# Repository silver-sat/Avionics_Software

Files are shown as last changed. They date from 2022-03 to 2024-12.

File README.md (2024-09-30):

# Avionics_Software
This is the SilverSat Avionics board code base, including software for team meeting discussions.

The Avionics Board shares many characteristics with the 
Adafruit Metro M0 Express and in general testing can be performed on either board. However, the standard Arduino Metro M0 Express configuration has fewer serial ports and 
fewer I2C buses than the Avionics Board. Also, serial ports, I2C devices, and digital IO ports 
have different pin locations on the boards. The variants folder in this repository has instructions and configuration files for setting up Metro M0 Express boards with additional serial ports and I2C buses and for setting up the Avionics Board hardware.

## Mock Hardware Drivers
The "AvionicsTesting1" folder contains mock hardware drivers for the components on the Avionics Board. These drivers act as simulated and simplified interfaces for the hardware on the board. They are configured as Arduino libraries.

You can install these libraries by cloning the repository using git or by downloading a .zip file containing the libraries and extracting the folders. Copy the desired libraries into your Ardunio libraries folder.

The interfaces to the mock hardware are designed to be similar to those planned for the flight hardware and software. You can write tests and application software with the expectation of using similar driver interfaces for the flight implementation.

Each library contains an example using the interface to access the mock device. The repository also includes a sketch that exercises each of the mock interfaces.

## Hardware Unit Test Drivers
The "AvionicsTesting2" folder contains test drivers for the hardware components on the Avionics Board. These drivers can be used to verify and exercise the actual devices attached to a Metro M0 or on the board.

You can install these drivers by cloning the repository using git or by downloading a .zip file containing the drivers and extracting the sketches. Follow the instructions in the variants folder to setup the right pin configurations for your environment. If you are using the Avionics Board hardware, define ```CRYSTALLESS``` in the appropriate Arduino core ```startup.c``` file. (The Avionics Board does not have a crystal.) 

You can exercise individual hardware components by building the related sketch (e.g. ```test_imu```) and uploading it to a Metro M0 or the Avionics Board. Note that some external libraries are required, for example to support the MPU6050 hardware. A full list of libraries is in the AvionicsTesting3 folder ```README.md```. Install required libraries following the normal Arduino procedure.

You can execute all of the hardware tests in sequence using a bash script provided in the "AvionicsTesting2" folder. This script requires the Arduino CLI, which can be installed following the instructions at https://arduino.github.io/arduino-cli/0.21/installation/. Make the script executable, connect a serial monitor to the appropriate port on the target board, open a terminal window on your development computer, 
and execute the script. Follow the prompts and observe the results in the serial monitor.

## Test Process Loop
The "AvionicsTesting3" folder "README.md" describes the board testing capabilites of the "test_process_loop" software and provides test setup instructions. The "test_process_loop" sketch in the folder implements the initialization, watchdog management, beacon transmission, command processing, and payload management functions for the Avionics Board.

## FlatSat Testing
The "FlatSat" folder "README.md" describes the flat sat testing capabilities of the "avionics_loop.ino" software and provides test setup instructions. The "avionics_loop.ino" sketch implements the software functions of the Avionics Board. Test routines are provided to test the ground commands received by the satellite and to test the local command interface to the Radio Board.

## Flight

The "Flight" folder "README.md" describes the flight software. This folder contains all of the software used by the flight Avionics Board as well as tests for the Day in the Life scenario and each of the commands recognized by the Avionics Board. The tests are designed for use with pytest and can be repeated automatically using the pytest-repeat plugin.

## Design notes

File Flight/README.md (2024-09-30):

## Avionics Loop
The "avionics" folder contains the Avionics Board software for operating the satellite. 
This includes the process loop, hardware drivers, command processor, and interface software for the antenna, power, radio, and payload boards.

### Test Drivers
The "test_satellite" folder contains drivers for testing the commands supported by the satellite and a "Day in the Life" test.

### Software
The "avionics.ino" sketch is the main process loop for operating the Avionics Board. In avionics.ino, the hardware devices on the Avionics Board are implemented as classes interfacing to real hardware. The other SilverSat boards: Antenna, Power, Radio, and Payload, are implemented as classes which interface with those boards. 

The local messages which Avionics sends to the Radio Board, the ground commands the Radio Board forwards to Avionics, and the responses Avionics sends to the Radio Board for forwarding to the ground are also represented as classes.

The Avionics Board connects to the Radio Board via the Serial1 interface. It connects to the realtime clock via the critical I2C connection. The Avionics Board connects to the IMU, the FRAM, the antenna, and the Power Board via a second I2C connection. Accessing the antenna and the Power Board require activation of an I2C switch. The Avionics Board connects to the Payload Board via digital IO lines.

### Libraries
The "avionics" folder includes an interface to the Arduino log library, which can be used to log status information. Adafruit libaries are used to support the I2C devices, the MPU6050, the FRAM, the real time clock.

### Setup
To setup a build environment, clone this repository to your computer or download a .zip file and extract the folders. Install the Adafruit MPU6050 and FRAM libraries with dependencies using the Arduino Library Manager. Install the ArduinoLog library by downloading it into your library folder. Compile and upload the "avionics.ino" sketch to the Avionics Board microcontroller using a J-Link programmer. There is no bootloader on the Avionics Board.

Review the other READMEs in this repository and ensure your environment is configured correctly. In particular, you will need variant files for the Avionics Board. You will need to define the Avionics Board as crystalless. You will need to modify the linker script to place the executable at location 0 and not leave space for a bootloader. You do not need to set up support for command signing as it has been deprecated.

The "avionics.ino" log level can be changed by modifying the "log.begin" method call in the "avionics_loop.ino" file. The "avionics.ino" file has instrumentation for tracking processing time and memory usage that is enabled by ```#define INSTRUMENTATION```. The log utility is used to display the instrumentation data.

The "avionics.ino" sketch receives commands and sends messages and local commands to and from the Radio Board via the "Serial1" port. It sends log data to the "Serial" port. After uploading your sketch, verify that the Avionics Board has initialized properly by opening a terminal connection to the "Serial" port and reviewing the log entries. Terminal emulators known to work include the Arduino IDE Serial Monitor, the VS Code Arduino extension Serial Monitor, and the tio terminal emulator. (```tio -b 57600 -m INLCRNL,ONLCRNL [portname]```). 

### Testing

You can use the "Serial1" port to send commands to the Avionics Board and observe the responses. The commands must be KISS formatted. Commands use utf-8 single-byte printable characters and can typically be generated by adding FEND [0xC0] at the beginning and end of the command. The first FEND must be following by the appropriate command byte as defined in https://docs.google.com/document/d/1Vwpk0ab0HoC62mU7A1fQwpmhmtmZO0VwPtXjQipe0v0/edit?usp=sharing. Be aware that the FENDs and command bytes are not printable characters. The Avionics Board implements the KISS escape processing protocol, although it is not currently in use.

The "test_satellite" folder includes Python programs for unit testing each of the Avionics Board commands and for a Day in the Life test. These programs are designed to be managed and executed using pytest. After resetting the microcontroller you may run the entire suite of tests by entering ```pytest``` on the command line while in the "test_satellite" directory. (Depending on your configuration, ```python3 -m pytest``` may be required.) pytest also allows selective execution of tests. See https://docs.pytest.org/ for additional information. You can repeat the tests with the pytest-repeat plugin.

In addition to using pytest, you can send and receive traffic on the Serial1 port using a USB adaptor device and tio. Configure tio to display the traffic as hex bytes. 

### Documentation

The SilverSat Avionics Board document in the repository provides an overview of the Avionics Board hardware, software and commands.

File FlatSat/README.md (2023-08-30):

## Avionics Loop
The "FlatSat" folder contains the Avionics Board software for testing and operating the FlatSat configuration. 
This includes the process loop, hardware drivers, command processor, and interface software for the power, radio, and payload boards.

### Test Drivers
The "FlatSat" folder contains drivers for testing
the serial interface with the Radio Board in the "test_avionics" folder. These drivers can be used to test each of the local command implementations that require communication between the Avionics Board and the Radio Board, such as getting radio status and changing radio settings. The test drivers can be used to test the beacon functions and the halt function.

The FlatSat folder also contains
unit test drivers for the command functions of the Avionics Board in the "test_avionics" folder. These drivers can be used to verify and exercise the functions of the Avionics board such as setting the realtime clock, telemetry collection, controlling beacon transmission, and triggering the watchdog.

Also in the "test_avionics" folder are drivers to test the interface with the Payload Board, Power Board, and Antenna. These drivers are augmented by simulators in the "payload_simulator", "eps_simulator", and "antenna_simulator" folders, which contain Python programs suitable for execution on an Adafruit Metro M0 (payload) and Adafruit Grand Central (eps and antenna). When appropriately connected, these simulators respond to the interfaces similarly to the actual devices, thus allowing testing without the entire Flatsat configuration. The folders also include simple programs for testing the simulators.

### Software
The "avionics_loop.ino" sketch is the main process loop for testing and operating the Avionics Board. In avionics_loop, the hardware devices on the Avionics Board are implemented as classes interfacing to real hardware. The other SilverSat boards: Power, Radio, and Payload, are implemented as classes which interface with those boards. 

The local messages which Avionics sends to the Radio Board, the ground commands the Radio Board forwards to Avionics, and the responses Avionics sends to the Radio Board for forwarding to the ground are also represented as classes.

The Avionics Board connects to the Radio Board via the Serial1 interface. It connects to the realtime clock via the critical I2C connection. The Avionics Board connects to the IMU, the FRAM, the antenna, and the Power Board via a second I2C connection. Accessing the antenna and the Power Board require activation of an I2C switch. The Avionics Board connects to the Payload Board via digital IO lines.

### Libraries
The "FlatSat" folder includes an interface to the Arduino log library, which can be used to log status information on the Radio Board Serial interface. Adafruit libaries are used to support the I2C devices, the MPU6050, the FRAM, the real time clock,  The Arduino Crypto library is used to support command signing.

### Setup
Signed commands require that the Avionics Board and the ground share a secret. This secret is defined as a sixteen-byte array. 

Following the Arduino convention, an "arduino_secrets.h" file is required to store the secret. It must ```#define``` a sixteen-byte array named ```SECRET_HASH_KEY```, which is compiled into the sketch. DO NOT upload "arduino_secrets.h" to github or other shared locations. The software used to generate signed commands must use an identical sixteen-byte secret. For these tests, the secret is stored in "secret.txt". DO NOT upload "secret.txt" to github. The "test_signing" folder located in the "AvionicsTesting3" folder in this repository includes a Python program, "make_secret.py", which can be used to generate shared secrets. If the secrets use by the Avionics Board and the test programs or ground software are not identical, command signing will fail.

To setup a test environment, clone this repository to your computer or download a .zip file and extract the folders. Generate a secret and create an "arduino_secrets.h" file and a "secret.txt" file to store it. Add both to your ```.gitignore``` to prevent them from being uploaded to github. Install the Adafruit MPU6050 and FRAM libraries with dependencies using the Arduino Library Manager. Install the ArduinoLog and Arduino Crypto libraries by downloading and copying them into your library folder. Compile and upload the "avionics_loop.ino" sketch to the Avionics Board microcontroller using the standard Arduino tools or alternative deployment tools.

The "avionics_loop.ino" sketch has extensive logging capabilities based on the ArduinoLog utility (https://github.com/thijse/Arduino-Log/). The log level can be changed by modifying the "log.begin" method call in the "avionics_loop.ino" file. 

The "avionics_loop.ino" file has instrumentation for tracking processing time and memory usage that is enabled by ```#define INSTRUMENTATION```. The log utility is used to display the instrumentation data.

The "avionics_loop" sketch receives commands and sends messages and local commands to and from the Radion Board via the "Serial1" port. It sends log data to the "Serial" port. After uploading your sketch, verify that the Avionics Board has initialized properly by opening a terminal connection to the "Serial" port and reviewing the log entries. Terminal emulators known to work include the Arduino IDE Serial Monitor, the VS Code Arduino extension Serial Monitor, and the tio terminal emulator. (```tio -m INLCRNL [portname]```). If you are using a bootloader, be aware that use of
a serial monitor can interfere with uploading. If you aren't using the Arduino toolset, disconnect your serial monitor software before using the bootloader.

### Testing

You can use the "Serial1" port to send commands to the Avionics Board and observe the responses. The commands must be KISS formatted. Since commands in general use utf-8 single-byte printable characters, commands can typically be generated by adding FEND [0xC0] at the front and end of the command. The first FEND must be following by the appropriate command byte as defined in https://docs.google.com/document/d/1Vwpk0ab0HoC62mU7A1fQwpmhmtmZO0VwPtXjQipe0v0/edit?usp=sharing. Be aware that the command bytes are not printable characters.

The Avionics Board implements the KISS escape processing protocol, although it is not currently in use.

The "FlatSat/test_avionics" folder includes python programs for unit testing each of the Avionics Board commands and for interfacing to the rest of the satellite. These programs are designed to be managed and executed using pytest. After resetting the microcontroller you may run the entire suite of tests by entering ```pytest``` on the command line while in the "FlatSat/test_avionics" directory. (Depending on your configuration, ```python3 -m pytest``` may be required.) 

pytest also allows selective execution of tests. See https://docs.pytest.org/ for additional information. Be sure to run the ```test_00_avionics_initialization.py``` test first any time the microcontroller is restarted to process the initialization messages. You can also review the startup messages in a serial monitor and then end the serial monitor session before running automated tests. To test signed commands, the "secret.txt" file must include the same secret as the "arduino_secrets.h" file used to build "avionics_loop.ino." The "utility.py" program in "avionics_test" contains functions to issue commands and to generate signed commands. 

You can observe traffic on the Serial1 port using a USB adaptor device and tio. ```tio -x [portname]``` will display the traffice as hex bytes. Note that this will interfere with the automated tests, so should only be used when manually entering commands on the (separate) Serial port. It may also be useful to open terminals showing output from the payload simulator and the eps/antenna simulator.

### Documentation

The SilverSat Avionics Board document in the repository provides an overview of the Avionics Board hardware, software and commands.

Documentation for the software and tests can be viewed by running doxygen (https://doxygen.nl/) using the provided Doxyfile and then opening docs/index.html in a browser. Modifications to the Doxyfile may be required to reflect your directory structure.

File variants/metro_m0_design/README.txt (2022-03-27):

This folder contains the variant files for the Adafruit Metro M0 Express to add 2 extra HW serial ports (3 total) and 1 extra wire port (2 total).

Put these in the appropriate variants folder.  For example on my system it was:

C:\Users\conra\AppData\Local\arduino15\packages\adafruit\hardware\samd\1.7.10\variants\metro_m0

The fritzing file "MetroVariantTest.fzz", shows roughly (I used cables instead of FTDI modules) how I connected to the Metro M0 to test the new ports.

I will be adding code (Arduino) later that supports the test.

I chose the two I2C devices simply based on what was lying on my bench at the moment, so there's nothing special about them.

For this variant:
Serial0 is on D11 (txd) and D13 (rxd)
Serial1 is on D1 (txd) and D0 (rxd) (default config)
Serial2 is on D6 (txd) and D7 (rxd) 
Wire uses SCL and SDA (by default, obviously)
Wire1 is on D4 (SDA) and D3 (SCL)

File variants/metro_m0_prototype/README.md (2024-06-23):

This folder contains the variant.cpp and variant.h files for the Adafruit Metro M0 used to prototype the SilverSat Avionics Board. 

These files are not compatible with the Avionics Board. To build Arduino sketches for the Avionics Board, see the avionics_board variants.

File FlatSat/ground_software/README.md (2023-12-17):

# Ground Control Software

The ground control software presents a user interface for entering commands to the satellite and receiving responses. It also enables the use of gpredict radio Doppler data for the ground radio.

The ground control software is a web application designed to run on a Flask development server in a single-threaded environment on a single laptop. It is not secured for network deployment and the serial link to the ground radio is not implemented for use in a multi-threaded environment.

## Installing the User Interface

Clone the Avionics_Software repository from github to a local directory on the laptop. If the repository is already present, ensure it is up to date using git pull or the equivalent.

Open a command shell and navigate to the ground_software directory in the FlatSat directory. Create a python virtual environment with the following command

```python3 -m venv .venv```

Activate the virtual environment with 

```. .venv/bin/activate```

Note that the .venv directory is a hidden file (it starts with "."), so you may have to use command line options or change the settings of your file manager to see it in a file listing.

Now install Flask using this command

```pip install Flask```

Python virtual environments are recommended for use with Flask, and may be required by your operating system. If you understand the implications, you may be able to install Flask at the system level using a package manager or other method.

Install pyserial using this command

```pip install pyserial```

Now move to the control directory in the ground_software directory and enter the following command

```Flask run --debug```

This starts the app.py application in the folder. If you receive an error message, you may need to modify the serial port name in app.py to match the port name on your system.

Open a browser and navigate to the address displayed, typically http://127.0.0.1:5000/

You may now enter commands to the satellite by clicking a button or typing a command on the command line.

## Installing the Radio Doppler Control

Install the gpredict application on the laptop following the instructions for the operating system.

The gpredict_radio_interface.py program in the radio folder and the Flask web application provide the functions of Hamlib rigctld daemon. You do not need rigctld to control the radio frequency.

Open a new command window, navigate to the radio folder, and enter the command

```gpredict_radio_interface.py```

The program will listen on the default TCP/IP port used by gpredict for radio frequency information.

Now launch gpredict, add a radio as explained in the User Manual, open the radio interface, select a satellite in Target and track it. Verify that the Flask application is running. Select your radio in Settings and engage it. Radio Doppler data for the selected satellite will be transmitted to the ground radio.

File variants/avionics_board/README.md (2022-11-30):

This folder contains the variant.cpp and variant.h files for the SilverSat Avionics Board. 

To build Arduino sketches for the Avionics Board or to test using a Metro M0, git clone or download a .zip file containing these files to your development computer. 
Create a hardware folder in your Arduino sketch folder as documented 
at https://arduino.github.io/arduino-cli/0.21/platform-specification/#hardware-folders-structure, copying the Adafruit Metro M0 Express
files as the hardware configuration template.

Rename the appropriate folders and make the necessary changes to boards.txt in the new folder structure. Copy variant.cpp and variant.h
into that folder structure, replacing the Metro M0 Express files with the same names.

As an example, on Ubuntu, create a "hardware" folder in your "Arduino" folder. Create an "avionics" folder in "hardware."
Copy the "samd/[version]" folder containing the Metro M0 definitions located at ".arduino15/packages/adafruit/hardware/samd/[version]" to 
your new "hardware" folder and rename it to "samd." (That is, drop the version level of the folder structure.) Rename the "metro_m0" folder in the 
"variants" folder and edit "boards.txt" to reflect the new name. Replace "variant.cpp" and "variant.h" in the renamed folder with the
downloaded files. Follow a similar process to create a Metro M0 configuration with additional serial ports and a second I2C bus for testing. 

If you do not have the Metro M0 Express definitions on your development computer, you can download them using the procedure
documented at https://learn.adafruit.com/adafruit-metro-m0-express/arduino-ide-setup.

Define ```CRYSTALLESS``` in the Avionics Board Arduino core startup.c file. (The Avionics Board does not have a crystal.) Do not make this change for Metro M0.

If you want to load software using a programmer and have no bootloader on the board, modify the "boards.txt" file to make "flash_without_bootloader.ld"
the linker script file base name. This provides reliability and convenience, but does require that you have a hardware programming device. Be aware that your program 
should be loaded at 0x2000 if using a bootloader and will likely be loaded at 0x0000 if not.

After you have setup the definitions for the Avionics Board, open your development environment, select the new board configuration, 
build your sketch, and upload it to the Avionics Board. See the instructions in the AvionicsTesting3 ```README.md``` for further information.

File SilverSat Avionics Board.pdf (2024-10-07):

# SilverSat Avionics Board

Software and Command Description

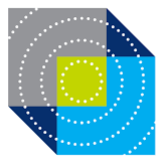
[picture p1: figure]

7 October 2024
Contact: lee@silversat.org

## INTRODUCTION

This document summarizes the hardware and software of the SilverSat Avionics Board. It briefly describes the interfaces with the SilverSat Power Board, Radio Board, Payload Board, and antenna. It also provides an overview of the commands received and sent by the Avionics Board.

1

## REVISION HISTORY

Version 1.0, Apr 11, 2023

Initial release

Version 1.1 Apr 14, 2023

Added command formats, reorganized sources

Version 1.2

Reformatted command outputs

Version 1.3 October 7, 2024

General update to reflect software changes

2

## TABLE OF CONTENTS

INTRODUCTION
REVISION HISTORY
TABLE OF CONTENTS
OVERVIEW
HARDWARE
SOFTWARE
INITIALIZATION
PROCESS LOOP
SOFTWARE ORGANIZATION
TESTING INFRASTRUCTURE
AVIONICS BOARD HARDWARE
MICROCONTROLLER
WATCHDOG
REAL TIMWATCHDOGE (https://docs.google.com/document/d/1S8KbOSXrL_yW1S88hW_mSTv4Je4pVHNBBO4vtaCxD2I/edit) CLOCK
INERTIAL MANAGEMENT UNIT
FRAM
POWER BOARD INTERFACE
RADIO BOARD INTERFACE
SATELLITE COMMANDS
GROUND COMMANDS
CHANGE SATELLITE STATE
COMMAND
PARAMETERS
DESCRIPTION
GET SATELLITE STATE
COMMAND
PARAMETERS
DESCRIPTION
INVOKE SATELLITE OPERATION COMMAND
PARAMETERS
DESCRIPTION
INVALID AND UNKNOWN COMMANDS COMMAND
PARAMETERS
DESCRIPTION

3

RADIO COMMANDS
COMMAND
PARAMETERS
DESCRIPTION
DEPRECATED COMMANDS
COMMAND
PARAMETERS
DESCRIPTION
COMMAND FORMATS
COMMAND
FORMAT
ACK
RESPONSE
LOCAL COMMANDS
COMMAND
VALUE
PAYLOAD BOARD INTERFACE
ANTENNA INTERFACE
SOURCES
TOOLS
LIBRARIES
REFERENCES
LEARNING

4

## OVERVIEW

SilverSat is an educational project for students in middle school and high school. The students are building and programming a 1U cubesat that will take photos from space and transmit them to a widely available media service, currently planned to be Twitter. SilverSat will launch from the International Space Station courtesy of an educational grant from NASA.

## HARDWARE

SilverSat hardware includes an EnduroSat structure surrounded by solar cells and four boards implementing the satellite capabilities. The boards are:

1. An EPS-I power board, also provided by EnduroSat, which stores power from the solar cells surrounding the structure and manages the distribution of power to the satellite
2. An Avionics Board, described in this document, which manages the timing of photo and communications on the Payload Board, processes commands from the ground, and manages the timing and content of beacon broadcasts
3. A Radio Board, which manages communications between the satellite and the ground station
4. A Payload Board, which captures images and communicates them to a media service, currently Twitter.

The Avionics Board, the Radio Board, and the Payload Board are developed and implemented by SilverSat. The antenna used by the satellite is provided by EnduroSat.

This document focuses on the hardware and software located on and accessed by the Avionics Board, including its microcontroller, watchdog timer, realtime clock, inertial measurement unit, and ferroelectric random-access memory. It also describes the interfaces to the Power Board, the Radio Board, the Payload Board, and antenna.

## SOFTWARE

The software running on the Avionics Board implements initialization, services the watchdog, manages beacon timing, executes commands from the ground, and controls the Payload Board. The software is implemented using the Arduino software

5

environment and is based on the standard setup() and loop() functions provided by Arduino.

### INITIALIZATION

When power is applied to the Avionics Board, the avionics loop software starts the Serial and logging functions used for board software development, monitoring, and testing. These functions may not be used in the flight software, depending on the final checkout procedures selected by the team.

The avionics loop then initializes the Avionics Board and the interfaces to the Power Board, the Radio Board, and the Payload Board.

The Avionics Board then pauses for a predefined deployment delay interval. In the flight software, this delay will be 45 minutes.

After the delay interval, the Avionics Board deploys the antenna, waiting to verify that deployment is successful. In sequence, the Avionics Board attempts two deployments using the I2C interface to the antenna and signals the Radio Board to attempt two deployments using a direct connection to the antenna. Initialization proceeds when the antenna shows that it has been opened successfully.

The Avionics Board then commences its standard process loop.

### PROCESS LOOP

The process loop, instantiated in the Arduino loop() function in avionics_loop.ino, includes the following steps:

1. Determine whether the process is within the watchdog window. If so, trigger the watchdog.
2. Check the IMU to determine whether the satellite is stable.
3. Determine whether the beacon interval has elapsed. If so, send a beacon.
4. Determine whether a command has arrived from the ground or the Radio Board. If so, process the command.
5. Determine whether it is time to take a photo. If so, signal the Payload Board to take the photo.
6. Determine whether the Payload Board is requesting a shutdown. If so, turn off power to the Payload Board after a delay.

The process then repeats.

### SOFTWARE ORGANIZATION

6

In addition to the overall structure provided by the Arduino setup() and loop() functions in the avionics.ino file, the software is organized into classes providing the required capabilities. Most classes are declared in a header file and defined in a cpp file. The exceptions are the Beacon, Message, and Response classes which are header only.

The PowerBoard, AvionicsBoard, RadioBoard, PayloadBoard, and Antenna functions and data are defined as classes.

Hardware such as the EPS-I power supply and the DS1337 real time clock are defined as classes. Some hardware has an additional abstraction and encapsulation layer, for example the PowerBoard and the ExternalRTC, respectively, for the devices just noted. This is also the case for the ExternalWatchdog and the IMU.

Command processing is controlled by the CommandProcessor class, which acquires commands from the RadioBoard, validates and parses them and retrieves a command object from the CommandWarehouse class. The CommandProcessor then executes the acknowledgement and processing methods in the command object, taking advantage of the virtual function capability provided by the C++ language.

The log_utility class generates standard log entries to support the development process. Logging will not be included in the flight software unless it is required for final testing after the vibration test.

### TESTING INFRASTRUCTURE

The silver-sat/Avionics_Software github repository contains versions of the software used for prototyping, unit testing, and function testing in the AvionicsTesting1, AvionicsTesting2, and AvionicsTesting3 directories. The readme files in those directories provide additional information.

The FlatSat testing version of the software is located in the FlatSat directory in the repository. In addition to the avionics_loop software, it also contains test simulators for the Antenna, the Power Board, and the Payload Board. An extensive set of tests for initialization, board interfaces, commands, and error conditions are located in the test_avionics directory.

The Flight directory contains the flight version of the software, implemented with avionics.ino as the main sketch. Test cases are provided in the test_satellite directory.

These tests are structured to be run as a complete set beginning with board initialization or can be run individually. They are written in Python and use pytest as the test driver. A

7

common.py module provides convenience functions. Instructions for setting up and executing the tests are in the readme.

Also present in the repository is a Doxygen file that can be used to generate detailed documentation of the software. Again, instructions are in the readme.

## AVIONICS BOARD HARDWARE

The Avionics Board hardware is defined in the Avionics Board (https://github.com/silver-sat/Avionics_Board.git) repository.

The microcontroller is a Microchip SAMD21G18 32-bit Cortex-M0+ with 256K of flash and 32K of random access memory. The microcontroller runs the avionics loop software in the Arduino runtime environment. The Avionics Board includes an external Texas Instruments TPS3813-Q1 watchdog timer, a Maxim Integrated DS1337 real time clock, an Adafruit MPU-6050 inertial management unit, an Infineon Technologies 32K byte CT15B256J ferroelectric random access memory, and switches to control access to external I2C devices and two serial links. The critical I2C for the realtime clock and the microcontroller serial link are always enabled.

### MICROCONTROLLER

The microcontroller pins are defined in the Arduino variant.h and variant.cpp files in the repository. There is no crystal on the Avionics Board, and the Ardunio environment must be configured to reflect that. The microcontroller software can use a bootloader or can be programmed with a hardware device.

If a bootloader is used, it must be aware of the watchdog and either trigger or disable it during program loading. The load address of the software must be updated to reflect the presence or absence of a bootloader. Recent versions of the software have used a J-Link EDU Mini to program the Avionics Board to avoid problems with the bootloader and watchdog interaction.

A timer in the microcontroller is used for beacon interval timing. The internal real time counter is not used in this capacity, thus enabling beacons before the clock is set. The internal watchdog in the microcontroller is not used.

### WATCHDOG

The external watchdog provides a lower bound and an upper bound for a window and must be triggered within the window to prevent a reset. Because the watchdog is always active, the appropriate resistor must be shorted to enable software loading on the flight

8

hardware.

### REAL TIME CLOCK

The DS1337 provides real time clock (RTC) services for the satellite, specifically payload photo timing. Since there is no power available when the satellite is in transit to orbit, the clock must be set by a ground command after the satellite is deployed. The SetClock command serves this purpose.

### INERTIAL MANAGEMENT UNIT

The inertial management unit (IMU) is an accelerometer and gyroscope combination. It is used to determine the stability of the satellite. Stability status is transmitted in the beacon and can be retrieved with the GetTelemetry command.

### FRAM

The ferroelectric random access memory (FRAM) is initialized but not used by the Avionics Software.

## POWER BOARD INTERFACE

The Power Board stores, transfers and distributes power generated by the solar panels. The firmware on the Power Board manages the power flow and battery heaters as required. The Avionics Board reads Power Board status via the non-critical I2C bus from the board and transmits it to the ground in response to ground commands (GetPower) and in the power beacon character.

The Power Board has an I2C interface to modify its operation. That interface is use to set the status of some power lines and to cycle power for the Radio Board should the be required. The Power Board also has an interface implementing the EnduroSat satellite management communications protocol. That interface and protocol are not used.

## RADIO BOARD INTERFACE

The Avionics Board communicates with the Radio Board over the Serial1 interface. Avionics receives commands from the ground, sends local commands to the Radio Board, receives ACKs and RESponses to those local commands, and receives local commands from the Radio on the interface.

This interface is always active and the Avionics Board expects traffic to occur at any time.

9

Ground commands are collected and the digital signature is validated. The command is then parsed, validated and executed. Some commands generate local traffic with the Radio Board.

The Avionics Board sends a local status request to the Radio Board when a GetComms command is received from the ground station. It sends a local halt command upon receipt of a TweeSlee command.

The Avionics Software also sends beacon local commands to the Radio Board, which adds its status character before transmitting the beacon in morse code. During initialization, the Avionics Software will direct the Radio Board to execute the backup antenna deployment procedure should it be required.

The Avionics Board sends local commands to the Radio Board on receipt of the radio command shown in the table below.

The Radio Board sends a local response to the status request and radio commands. The Avionics Board converts these responses into messages and forwards them to the ground (via the radio).

The Radio can send a local command to Avionics if it requires a power cycle.

## SATELLITE COMMANDS

### GROUND COMMANDS

Commands are transmitted from the ground, through the ground and satellite radios, and then to the Avionics Board via the Serial1 interface.

Commands are KISS encoded and KISS escaped, although the current implementation does not require escapes since commands and arguments are UTF-8 encoded text.

Each ground command arriving at the satellite will have the second byte (after the initial FEND) set to 0xAA to distinguish it from local traffic, which has a second byte of 0x00. Local traffic includes radio responses to commands from the Avionics Board to the Radio Board and the reverse. These commands and responses are described in the Silversat Local Commands (https://docs.google.com/document/d/1Vwpk0ab0HoC62mU7A1fQwpmhmtmZO0VwPtXjQipe0v0/edit?usp=sharing) document.

Ground commands are case sensitive and shown in the tables below. Arguments are UTF-8 encoded and blank separated.

10

Ground commands are signed to insure integrity. They consist of a 32-byte HMAC, an 8-byte salt, a 4-byte sequence number, and the command. The HMAC, salt, and sequence are converted to the UTF-8 representation of their hex values for transmission. They double in length under this transformation.

Ground commands sent to the Avionics Board receive an ACK and a RESponse, which is dependent on the command. Invalid and unknown commands, including those with the wrong number or type of parameters, may receive a NACK rather than an ACK and no response. Commands can receive an ACK and fail to execute.

Command length is limited to 256 bytes or the available space in the frame buffer.

## CHANGE SATELLITE STATE

COMMAND | PARAMETERS | DESCRIPTION
SetClock | Year, month, day, hour, minute, second: integers in UTF-8 encoding | Set realtime clock
BeaconSp | Interval in seconds: integer in UTF-8 encoding | Set beacon spacing
PicTimes | Year, month, day, hour, minute, second: integers in UTF-8 encoding | Set time for photos; queue length is 5
ClearPicTimes | | Empty PicTimes queue
UnsetClock | | Unset the real time clock

## GET SATELLITE STATE

COMMAND | PARAMETERS | DESCRIPTION
ReportT | | Respond with real time clock setting; subsumes GetTime

11

GetPicTimes | Respond with photo schedule
GetTelemetry | Respond with telemetry
GetPower | Respond with power status
GetComms | Respond with Radio Board status
GetBeaconInterval | Respond with beacon interval

## INVOKE SATELLITE OPERATION

COMMAND | PARAMETERS | DESCRIPTION
NoOperate | | Acknowledge; subsumes Ping
SendTestPacket | | Reply with test message
PayComms | | Start Payload Board in communications mode; subsumes Begin tweet
TweeSlee | | Stop Payload Board activity; subsumes Halt
Watchdog | | Force watchdog timeout

## INVALID AND UNKNOWN COMMANDS

COMMAND | PARAMETERS | DESCRIPTION
Invalid | | Invalid; used for testing
Unknown | | Unknown; command not

12

recognized

## RADIO COMMANDS

COMMAND | PARAMETERS | DESCRIPTION
ModifyMode | Mode index: 1 UTF-8 digit | Modify radio mode

## DEPRECATED COMMANDS

COMMAND | PARAMETERS | DESCRIPTION
Halt | | See TweeSlee
s_call_sig | | Set call sign
g_call_sig | | Get call sign
GetPhotos (GPC) | | Reply with photo count
ModifyFrequency | Frequency: 9 UTF-8 digits | Modify radio frequency
AdjustFrequency | Frequency: 9 UTF-8 digits | Adjust radio frequency temporarily
TransmitCW | Duration: 2 UTF-8 digits | Transmit carrier wave
BackgroundRSSI | Duration: 2 UTF-8 digits | Report average RSSI
CurrentRSSI | | Report current RSSI
SweepTransmitter | Start frequency: 9 UTF-8 digits, stop frequency: 9 UTF-8 digits, steps: 3 UTF-8 digits, dwell: 3 UTF-8 digits | Transmit carrier over range of frequencies

13

SweepReceiver | Start frequency: 9 UTF-8 digits, stop frequency: 9 UTF-8 digits, steps: 3 UTF-8 digits, dwell: 3 UTF-8 digits | Measure RSSI over range of frequencies
QueryRegister | Register: 5 UTF-8 digits | Report register value

## COMMAND FORMATS

COMMAND | FORMAT | ACK | RESPONSE
SetClock (SRC) | "SetClock" + ' ' + year + ' ' + month + ' ' + day + ' ' + hour + ' ' + minute + ' ' + second Arguments are decimal integers in UTF-8 encoding and extra blanks are ignored | "ACK " + last good command sequence number | "RES SRC"
BeaconSp (SBI) | "BeaconSp" + ' ' + interval Interval in seconds: decimal integer in UTF-8 encoding | "ACK " + last good command sequence number | "RES SBI"
PicTimes (SPT) | "PicTimes" + ' ' + year + ' ' + month + ' ' + day + ' ' + hour + ' ' + minute + ' ' + second Arguments are decimal integers in UTF-8 encoding | "ACK " + last good command sequence number | "RES SPT"
ClearPicTimes (CPT) | "ClearPicTimes" | "ACK " + last good command | "RES CPT"

14

| | sequence number
UnsetClock (URC) | "UnsetClock" | "ACK " + last good command sequence number | "RES URC"
ReportT (GRC) | "ReportT" | "ACK " + last good command sequence number | "RES GRC " + ISO 8601 timestamp in UTF-8 encoding
GetPicTimes (GPT) | "GetPicTimes" | "ACK " + last good command sequence number | "RES GPT " + Zero or more timestamps in UTF-8 encoding
GetTelemetry (GTY) | "GetTelemetry"

"ACK " +
last good
command
sequence
number

"RES GTY" +
" AX " + x-axis
acceleration +
" AY " + y-axis
acceleration +
" AZ " + z-axis
acceleration +
" RX " + x-axis
rotation +
" RY " + y-axis
rotation +
" RZ " + z-axis
rotation +
" T " + temperature

Values are floating
point, UTF-8
encoded.
Acceleration is in
meters per second
per second. Rotation
is in radians per
second.
Temperature is in
degrees Celsius.

15

GetPower (GPW) "GetPower"

"ACK " +
last good
command
sequence
number

"RES GPW" +
" BBV " + battery
voltage +
" BBC " + battery
current +
" TS1 " +
temperature of
sensor 1 +
" TS2 " +
temperature of
sensor 2 +
" TS3 " +
temperature of
sensor 3 +
" 5VC " + 5 volt
current +
" H1S " + heater 1
state +
" H2S " + heater 2
state +
" H3S " + heater 3
state

Values are floating
point, UTF-8
encoded. Voltage is
in volts. Current is
in Amperes.
Temperature is in
degrees Celsius.
Heater state is true
or false.
GetComms (GRS) | "GetComms" | "ACK " + last good command sequence number | "RES GRS " + (data to be defined by the Radio Board team)
GetBeaconInterval (GBI) | "GetBeaconInterval" | "ACK " + last good command sequence number | "RES GBI " + interval Value is an integer. Interval is in seconds.

16

NoOperate (NOP) | "NoOperate" | "ACK " + last good command sequence number | "RES NOP"
SendTestPacket (STP) | "SendTestPacket" | "ACK " + last good command sequence number | "RES STP test"
PayComms (PYC) | "PayComms" | "ACK " + last good command sequence number | "RES PYC"
TweeSlee (TSL) | "TweeSlee" | "ACK " + last good command sequence number | "RES TSL"
Watchdog (WDG) | "Watchdog" | "ACK " + last good command sequence number | "RES WDG"
ModifyMode (RMM) | "ModifyMode" + ' ' + index Index is 1 decimal UTF-8 digit | "ACK " + last good command sequence number | "RES RMM " + index Index is 1 decimal UTF-8 digit

Extra blanks are ignored in all commands.

All messages are KISS encoded and start and end with a FEND. The command byte is 0xAA for commands received from the ground and 0xAA for ACKs, NACKs, and RESponses sent to the ground. Local commands are described below.

Commands may return a NACK and no response or the error response "RES ERR" if an error is encountered. NACKs are followed by the last good command sequence number if appropriate.

17

### LOCAL COMMANDS

Local commands are sent from the Avionics Board to the Radio Board and from the Radio Board to the Avionics Board via the Serial1 interface.

Commands are KISS encoded and KISS escaped, although the current implementation does not require escapes since commands and arguments are UTF-8 encoded text.

Each local command will have the second byte (after the initial FEND) set to 0x00 for local ACKs, local NACKs, and local RESponses, or to one of the values in the table below.. These commands and responses and the command arguments are described in detail in the Silversat Local Commands (https://docs.google.com/document/d/1Vwpk0ab0HoC62mU7A1fQwpmhmtmZO0VwPtXjQipe0v0/edit?usp=sharing) document.

The Avionics Board does not send local ACKs, local NACKs, or local RESponses. It ignores local ACKs and NACKs.

Commands arguments are UTF-8 encoded and blank separated.

Command length is limited to 256 bytes or the available space in the frame buffer.

Local commands are not digitally signed.

COMMAND | VALUE
Local Frame | 0x00
Remote Frame | 0xAA
Beacon | 0x07
Release Antenna | 0x08
Get Status | 0x09
Halt | 0x0A
Modify Mode | 0x0C

18

Cycle Radio 5V | 0x0F

## PAYLOAD BOARD INTERFACE

The Avionics Board communicates with the Payload Board via nine digital IO pins. The three input pins are voted, and the board determines state based on the majority of the pins.

Upon startup, the Avionics Board sets the "payload on" output pins high, or off. The hardware sets the "shutdown" pins high, or shutdown requested.

When the time for a picture arrives, or when the ground sends a command to communicate, the Avionics Board sets the payload "states" pins appropriately and then seat the three payload on pins low.. These pins are then voted on the Payload Board and power is enabled. The Avionics Board then monitors the shutdown lines. When they go low, it is an indication that the Payload Board is in user state.

When the Payload Board has completed its work, it raises the three shutdown pins. Again, the three shutdown pins are majority voted. When the Avionics Board senses the shutdown request, it delays a predetermined interval to allow the Payload Board to complete shutdown, then turn off the payload power.

The Avionics Board monitors for Payload Board sessions exceeding a maximum time and for a Payload over current fault.

## ANTENNA INTERFACE

The Avionics Board communicates with the antenna via the external I2C interface.

During startup, the Avionics Board initializes the satellite, waits for the deployment delay, then executes the antenna deployment protocol. Antenna Algorithm 1 is executed for all doors. The Avionics Board then waits for a predetermined period and reads the status of the doors. If all are open, execution proceeds.

If one or more doors are closed, the Avionics Board executes Antenna Algorithm 2 for all of the doors. It then waits a predetermined interval and reads the status of the doors. If all are open, execution proceeds.

If one or more doors are closed, the Avionics Board sends a local command to the Radio

19

Board to execute the backup antenna deployment procedure. If one or more doors are closed, the Avionics Board sends a second local command to the Radio Board to execute an alternate backup deployment procedure.

## SOURCES

### TOOLS

Arduino IDE https://www.arduino.cc/en/software

Arduino CLI https://blog.arduino.cc/2020/03/13/arduino-cli-an-introduction/

Visual Studio Code https://code.visualstudio.com/

KiCad https://www.kicad.org/

pytest https://docs.pytest.org/en/7.3.x/

Doxygen https://www.doxygen.nl/

### LIBRARIES

Arduino Log https://github.com/thijse/Arduino-Log

Arduino Cryptography https://rweather.github.io/arduinolibs/crypto.html

### REFERENCES

SilverSat https://silversat.org/

Avionics Board Hardware https://github.com/silver-sat/Avionics_Board

Avionics Board Software https://github.com/silver-sat/Avionics_Software

SilverSat Local Commands
https://docs.google.com/document/d/1Vwpk0ab0HoC62mU7A1fQwpmhmtmZO0VwPtXjQipe0v0/edit?usp=sharing (https://docs.google.com/document/d/1Vwpk0ab0HoC62mU7A1fQwpmhmtmZO0VwPtXjQipe0v0/edit?usp=sharing)

SilverSat github https://github.com/silver-sat

The Power Board and Antenna description documents are held under a non-disclosure agreement with EnduroSat.

KISS Protocol http://www.ax25.net/kiss.aspx

20

Arduino Language https://www.arduino.cc/reference/en/

SAMD21 Datasheet
https://ww1.microchip.com/downloads/en/DeviceDoc/SAM_D21_DA1_Family_DataSheet_DS40001882F.pdf (https://ww1.microchip.com/downloads/en/DeviceDoc/SAM_D21_DA1_Family_DataSheet_DS40001882F.pdf)

Watchdog Datasheet
https://www.ti.com/lit/ds/symlink/tps3813-q1.pdf?ts=1681244431222&ref_url=https%253A %252F%252Fwww.google.com%252F (https://www.ti.com/lit/ds/symlink/tps3813-q1.pdf?ts=1681244431222)

Real Time Clock Datasheet
https://www.analog.com/media/en/technical-documentation/data-sheets/ds1337-ds1337c. pdf (https://www.analog.com/media/en/technical-documentation/data-sheets/ds1337-ds1337c.pdf)

Inertial Management Unit Overview https://learn.adafruit.com/mpu6050-6-dof-accelerometer-and-gyro

Ferroelectric Random Access Memory Datasheet https://www.infineon.com/dgdl/Infineon-CY15B256J-SXE-DataSheet-v04_00-EN.pdf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 (https://www.infineon.com/dgdl/Infineon-CY15B256J-SXE-DataSheet-v04_00-EN.pdf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)

Wikipedia ASCII Definition https://en.wikipedia.org/wiki/ASCII

CPP Reference https://en.cppreference.com/w/

Python.org https://www.python.org/

### LEARNING

Adafruit https://www.adafruit.com/

Learn CPP https://www.learncpp.com/

CircuitPython https://circuitpython.org/

21

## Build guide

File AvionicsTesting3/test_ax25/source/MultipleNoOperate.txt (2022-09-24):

S>D:NoOperate
S>D:NoOperate
S>D:NoOperate
S>D:NoOperate
S>D:NoOperate
S>D:NoOperate
S>D:NoOperate
S>D:NoOperate
S>D:NoOperate
S>D:NoOperate
S>D:NoOperate
S>D:NoOperate
S>D:NoOperate
S>D:NoOperate
S>D:NoOperate
S>D:NoOperate
S>D:NoOperate
S>D:NoOperate
S>D:NoOperate
S>D:NoOperate
S>D:NoOperate
S>D:NoOperate
S>D:NoOperate
S>D:NoOperate
S>D:NoOperate
S>D:NoOperate
S>D:NoOperate
S>D:NoOperate
S>D:NoOperate
S>D:NoOperate
S>D:NoOperate
S>D:NoOperate
S>D:NoOperate
S>D:NoOperate
S>D:NoOperate
S>D:NoOperate
S>D:NoOperate
S>D:NoOperate
S>D:NoOperate
S>D:NoOperate
S>D:NoOperate
S>D:NoOperate
S>D:NoOperate
S>D:NoOperate
S>D:NoOperate
S>D:NoOperate
S>D:NoOperate
S>D:NoOperate
S>D:NoOperate
S>D:NoOperate

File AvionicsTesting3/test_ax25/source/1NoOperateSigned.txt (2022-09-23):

S>D:1|0a74fd346e057103b8cf1b92bebd3585|NoOperate|4a026969b76a2f9c4177c4e8e708a530ea7fdc455ce8bd524fe9a75d17f29a27

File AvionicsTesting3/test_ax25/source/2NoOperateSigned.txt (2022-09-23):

S>D:2|a94e0435a56e9797bb942f5e517475fd|NoOperate|522d304ddb576e321bff054e30af9ad08355a2290a9e5d6d8e4006cd03f4b010

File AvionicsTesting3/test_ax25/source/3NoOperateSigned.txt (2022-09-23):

S>D:3|f746d02b30284824268e700923ef4951|NoOperate|bfd335483dd174c92885cd11222f5164d34ad15b45526e53207fc324c3f1156c

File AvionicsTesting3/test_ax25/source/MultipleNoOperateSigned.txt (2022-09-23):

S>D:1|0a74fd346e057103b8cf1b92bebd3585|NoOperate|4a026969b76a2f9c4177c4e8e708a530ea7fdc455ce8bd524fe9a75d17f29a27
S>D:2|a94e0435a56e9797bb942f5e517475fd|NoOperate|522d304ddb576e321bff054e30af9ad08355a2290a9e5d6d8e4006cd03f4b010
S>D:3|f746d02b30284824268e700923ef4951|NoOperate|bfd335483dd174c92885cd11222f5164d34ad15b45526e53207fc324c3f1156c

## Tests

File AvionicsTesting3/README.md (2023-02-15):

## Test Process Loop
The AvionicsTesting3 folder contains unit test drivers for the command functions of the SilverSat Avionics Board. These drivers can be used to verify and exercise the functions of the board such as setting the realtime clock, telemetry collection, controlling beacon transmission, triggering the watchdog, and starting a Twitter session on the mock Payload Board.

The test_process_loop sketch is the main process loop for testing the Avionics Board. Software in the other subfolders is used to support development and testing of the test loop. In test_process_loop, the hardware devices on the Avionics Board are implemented as classes interfacing to real hardware. The other SilverSat boards: Power, Radio, and Payload, are implemented as mock devices in software for these tests. Each mock board performs a subset of the functionality provided by the actual board as needed to test the Avionics Board.

The beacon and other local commands which Avionics sends to the Radio Board, the ground commands the Radio Board forwards to Avionics, and the messages Avionics sends to the Radio Board for forwarding to the ground are also represented as classes.

### Setup
An "arduino_secrets.h" file is required to store the secret shared with the ground station for command signing. It must ```#define``` a sixteen-byte array named ```SECRET_HASH_KEY```, which is compiled into the sketch. DO NOT upload "arduino_secrets.h" to github. The software used to generate signed commands must use an identical sixteen-byte secret. For these tests, the secret is stored in "secret.txt". DO NOT upload "secret.txt" to github. The test_signing folder includes a Python program, "make_secret.py", which can be used to generate shared secrets. If the secrets are not identical, command signing will fail.

To setup a test environment, clone this repository to your computer or download a .zip file and extract the folders. Generate a secret and create an "arduino_secrets.h" file and a "secret.txt" file to store it. Add both to your ```.gitignore``` to prevent them from being uploaded to github. Install the Adafruit MPU6050 and FRAM libraries with dependencies using the Arduino Library Manager. Install the ArduinoLog and Arduino Crypto libraries by downloading and copying them into your library folder. Compile and upload the test_process_loop sketch to the Avionics Board microcontroller using the standard Arduino tools or alternative deployment tools.

The test_process_loop sketch has extensive logging capabilities based on the ArduinoLog utility (https://github.com/thijse/Arduino-Log/). The log level can be changed by modifying the log.begin method call in the "test_process_loop.ino" file. The "test_process_loop.ino" file has instrumentation for tracking processing time and memory usage that is enabled by ```#define INSTRUMENTATION```.

The test_process_loop sketch receives commands and sends messages and local commands via the "Serial1" port. It sends log data to the "Serial" port. After uploading your sketch, verify that the Avionics Board has initialized properly by opening a terminal connection to the "Serial" port and reviewing the log entries. Terminal emulators known to work include the Arduino IDE Serial Monitor, the VS Code Arduino extension Serial Monitor, and the tio terminal emulator. (```tio -b 115200 -m INLCRNL,ONLCRNL [portname]```). If you are using a bootloader, be aware that use of
a serial monitor can interfere with uploading. If you aren't using the Arduino toolset, stop your serial monitor before using the bootloader.

### Testing

You can use the "Serial1" port to send commands to the Avionics Board and observe the responses. The commands must have AX.25 message headers and be KISS formatted. The DireWolf (https://github.com/wb2osz/direwolf) "kissutil" program does this formatting and is useful for entering commands manually. For example, you can launch kisstutil and type ```S>D:NoOperate``` at the prompt to send a NoOperate command to the Avionics Board. 

kissutil can also send messages stored in a file. Sample unsigned and signed command files are provided in the "test_ax25/source" folder. The signed commands are examples and do not incorporate your shared secret--they will not work with your compiled test_process_loop. 
You will need to replace the example signed commands with commands generated using your shared secret for command validation to succeed. The test_signing folder includes a Python program, "sign_command.py", which can be used to generate signed commands. The "secret.txt" file must contain the same secret as the "arduino_secrets.h" file compiled into your test_process_loop sketch. Signed commands require a sequence number which can be specified as a parameter to the program.

You can then launch kissutil, specifying the ```-f``` option for the "test_ax25/active" directory, and then copy commands from the "test_ax25/source" directory to the "test_ax25/active" directory to transmit them. Command files are deleted from the "test_ax25/active" folder after transmission. 

The AvionicsTesting3/test_commands folder includes python programs for unit testing each of the Avionics Board commands. These programs are designed to be managed and executed using pytest. After resetting the microcontroller you may run the entire suite of command unit tests by entering ```pytest``` on the command line while in the AvionicsTesting3 directory. pytest also allows selective execution of tests. See https://docs.pytest.org/ for additional information. Be sure to run the ```test_avionics_initialization.py``` test first any time the microcontroller is restarted to process the initialization messages. You can also review the startup messages in a terminal and then end the terminal session before running automated tests. To test signed commands, the "secret.txt" file must include the same secret as "arduino_secrets.h."

### Documentation

Documentation for the software and tests can be viewed by running doxygen (https://doxygen.nl/) using the provided Doxyfile and then opening docs/index.html in a browser. Modifications to the Doxyfile may be required to reflect your directory structure.

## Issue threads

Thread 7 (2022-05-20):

FRAM Test does not validate that data is maintained during a power loss

lcongdon, 2022-05-20:
The current FRAM prototype test does not include powering off the FRAM and verifying that the data persists.

lcongdon, 2022-05-22:
This problem is fixed in the Arduino version of the prototype

Closed 2023-05-07.

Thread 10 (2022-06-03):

FRAM Arduino Prototype fails on UNO

lcongdon, 2022-06-03:
Requires changes to integer data types

lcongdon, 2022-06-03:
Fixed by PR#11

Closed 2022-06-03.

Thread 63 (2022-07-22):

Initialize hardware tests for Avionics Board

lcongdon, 2022-07-22:
Modify the drivers and software to prepare for Avionics Board device unit testing

lcongdon, 2022-07-22:
Closed with #62

Closed 2022-07-22.

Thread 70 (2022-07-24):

Create process to run Avionics Board hardware unit tests in sequence

lcongdon, 2022-07-24:

lcongdon, 2022-07-24:
Requires updates to reflect pin addresses on Avionics Board

lcongdon, 2022-10-14:
Initial implementation in #71

lcongdon, 2022-10-17:
No longer required with automated command testing available

Closed 2022-10-17.

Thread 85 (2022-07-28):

Beacon timer does not wrap correctly

lcongdon, 2022-07-28:
Beacon timer fails when wrapping

Closed 2022-07-28.

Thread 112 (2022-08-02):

MPU6050 Initialization Succeeds if Device Not Attached

lcongdon, 2022-08-02:
Error message logged, but operation continues.

Closed 2022-08-11.

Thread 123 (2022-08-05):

Check for realtime clock status before throwing error

lcongdon, 2022-08-05:
Realtime clock currently requires setting before use, even if previously set

lcongdon, 2022-08-06:
Need a method to unset clock for testing

Closed 2022-08-12.

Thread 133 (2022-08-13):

Replace PCF8523 Realtime Clock with DS1337

lcongdon, 2022-08-13:
To test Avionics Board

lcongdon, 2022-10-16:
test_external_RTC.ino displays invalid date when using DS1307 driver.

Closed 2022-10-17.

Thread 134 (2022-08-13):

Replace Adafruit FRAM Breakout with CY15B256J FRAM

lcongdon, 2022-08-13:
To test Avionics Board

lcongdon, 2022-10-16:
test_FRAM.ino displays "Unexpected Manufacturer ID: 0x4" when accessed with Adafruit FRAM Breakout driver

Closed 2022-10-17.

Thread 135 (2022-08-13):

Update Pins from Metro M0 Express to Avionics Board pinouts

lcongdon, 2022-08-13:
Verify variant.h and variant.cpp and update code as required

lcongdon, 2022-10-14:
Serial ports, I2C buses, and SPI enabled by #179

lcongdon, 2022-10-22:
Closed by #196

Closed 2022-10-22.

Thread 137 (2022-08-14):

Handle Payload Over Current Signal

lcongdon, 2022-08-14:
Capture and handle Payload Board over current signal (GPIO 12 low on Avionics microcontroller). Log warning. Potentially cycle Payload Board power to recover.

Closed 2023-06-09.

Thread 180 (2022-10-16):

Header J1 pin 6 reads zero, should be one

lcongdon, 2022-10-16:
In test_SAMD21.ino, J1 pin 6 reads zero when connected to +3.3V. Suspect either bad pin numbering or issue in variant.cpp.

lcongdon, 2022-10-16:
Wiring error

Closed 2022-10-16.

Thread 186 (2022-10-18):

Real Time Clock yields bad time after processor reset

lcongdon, 2022-10-18:
Real time clock does not provide a valid time after the processor is reset. Does not occur with a power cycle.

lcongdon, 2022-10-18:
Works as expected with test program

lcongdon, 2022-10-18:
Closed by #189

Closed 2022-10-18.

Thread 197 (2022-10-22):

Transmit two FENDs on startup to clear buffer

lcongdon, 2022-10-22:
On startup, send two FENDs to the Radio Board to recover from a reset which causes an incomplete message

Closed 2022-10-22.

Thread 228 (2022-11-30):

Use Short Morse Code Characters for Beacon

lcongdon, 2022-11-30:
Use "short" Morse Code characters for beacon transmissions to reduce power consumption

lcongdon, 2023-02-07:
Beacon characters are not alphabetic

Closed 2023-02-07.

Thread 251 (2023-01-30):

Add Commands for Radio Board

lcongdon, 2023-01-30:

lcongdon, 2023-01-30:
Configure Radio to include CRC

lcongdon, 2023-01-30:
Configure Radio replaced. Modify Frequency and Modify Mode now include CRC32

Closed 2023-02-07.

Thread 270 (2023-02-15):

Implement Drivers for Payload Board Integration

lcongdon, 2023-02-15:

lcongdon, 2023-02-16:
[https://docs.google.com/document/d/1bUWdsmBf7PVzR7HwqF5asEHBNTsj_HKEqIgYk27C3FI/edit?usp=sharing](url) is the test plan

lcongdon, 2023-02-27:
Closed with #275

Closed 2023-02-27.

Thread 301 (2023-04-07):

Realtime Clock Error After Some Resets

lcongdon, 2023-04-07:
After some Avionics Board resets, the real time clock fails to initialize

Typically requires a power cycle to recover

lcongdon, 2023-05-08:
Disabled scan for DS1337 address

lcongdon, 2023-08-29:
Reenabled scans, no issues
Issue occurs for realtime clock and FRAM when attached to payload simulator

lcongdon, 2023-08-30:
Reproduced when processor reset during a read to the DS1337

lcongdon, 2023-09-10:
Closed for both I2C buses by #350

Closed 2023-09-10.

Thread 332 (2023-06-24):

Payload Board receives power while Avionics Board is starting up

lcongdon, 2023-06-24:
The Payload Board receives power for approximately the first two seconds of Avionics Board startup

lcongdon, 2023-06-28:
Now tracked as hardware issue

Closed 2023-06-28.

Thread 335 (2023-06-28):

No Error when EPS I not present at startup

lcongdon, 2023-06-28:
No error is generated when the EPS I is not present in the test configuration

lcongdon, 2023-07-09:
Battery voltage is shown as negative value in beacon, but zero when attempting to start communications session

Closed 2023-08-28.

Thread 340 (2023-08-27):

Implement Antenna Recovery if I2C commands fail

lcongdon, 2023-08-27:

lcongdon, 2023-08-30:
Closed by #346

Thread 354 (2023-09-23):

Respond to ground for unknown local antenna status command

lcongdon, 2023-09-23:

lcongdon, 2024-03-17:
Local command responses for radio status and radio modify mode cause a message to be sent to the ground. Every other local message (invalid commands, ACKs, NACKs, and other RESponses) are ignored.

Closed 2024-03-17.

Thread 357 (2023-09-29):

Avionics Board Enters Boot Loop

lcongdon, 2023-09-29:
The Avionics Board occasionally enters a boot loop.

Measurements of the power during this cycle show instability (very roughly from 1.5v to 3.3v)

Avionics log shows the event occurs after the MPU6050 initialization entry

Anomaly can occur one to many times

The problem is often resolved spontaneously

The problem occurs with both external power and with EPS I power

The problem has occurred whether the Payload Board has an SD card or not

The problem has occurred when the Radio Board is not attached to the FlatSat

lcongdon, 2024-08-27:
Issue has not recurred. Assume power problem in earlier hardware configuration.

Closed 2024-08-27.

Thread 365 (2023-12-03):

Resolve TXLED signal

lcongdon, 2023-12-03:

lcongdon, 2024-06-23:
Turned off LED by not defining PIN_LED_TXL in variants.h.

Closed 2024-06-23.

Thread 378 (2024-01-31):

Resolve Payload Board shutdown signal fault

lcongdon, 2024-01-31:
Change startup timeout from 90 seconds to 30 seconds

lcongdon, 2024-10-05:
Closed by #416

Closed 2024-10-05.

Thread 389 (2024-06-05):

Implement a Deadman Timer

lcongdon, 2024-06-05:
If the satellite is beaconing and doesn't hear from the ground for a period of time, stop the beaconing

lcongdon, 2024-06-09:
Already implemented

Closed 2024-06-09.

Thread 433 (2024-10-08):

Error: cannot initialize IMU after microcontroller hardware reset

lcongdon, 2024-10-08:
Occurs rarely when resetting with reset pin
Non-critical I2C bus appears clear

lcongdon, 2024-10-08:
No IMU was present

Closed 2024-10-08.

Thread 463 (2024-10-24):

Add total time since startup to log

lcongdon, 2024-10-24:
Consider adding to ground communication timer for beacon

lcongdon, 2024-10-28:
Should log handle register rollover?

lcongdon, 2024-11-03:
Days since startup added to log

Manually added changes from PR #482 to main branch, closed PR, deleted time branch

Closed 2024-11-03.

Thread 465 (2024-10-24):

Antenna reports Fatal error when open on initial test

lcongdon, 2024-10-24:

Closed 2024-10-24.

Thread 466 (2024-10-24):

Beacon not issued when antenna door is open

lcongdon, 2024-10-24:
With antenna door open on first attempt, beacon is skipped. Is antenna cycle complete flag set correctly?

lcongdon, 2024-10-24:
Closed by #468

Closed 2024-10-24.

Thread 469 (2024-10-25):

Power Board initialization should reflect error in startup

lcongdon, 2024-10-25:

lcongdon, 2024-11-05:
Closed by #485

Closed 2024-11-05.

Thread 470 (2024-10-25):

Radio Board initialization should reflect error in startup

lcongdon, 2024-10-25:

lcongdon, 2024-11-05:
Closed by #485

Closed 2024-11-05.

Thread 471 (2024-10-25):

Antenna initialization should reflect error in startup

lcongdon, 2024-10-25:

lcongdon, 2024-11-05:
Closed by #485

Closed 2024-11-05.

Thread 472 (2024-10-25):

Power Board shows inadequate power for photo session during startup testing

lcongdon, 2024-10-25:
This may also be an issue for SSDV and communications

Closed 2024-11-05.

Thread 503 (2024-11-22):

BackgroundRSSI and CurrentRSSI responses show sequence number, not command abbreviation

lcongdon, 2024-11-22:

lcongdon, 2024-11-22:
Log showed coincident sequence numbers from radio, not an issue

Closed 2024-11-22.

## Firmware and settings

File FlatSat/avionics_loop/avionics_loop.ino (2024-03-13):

/**
 * @file avionics_loop.ino
 * @author Lee A. Congdon (lee@silversat.org)
 * @brief Avionics Board Setup and Process Loop
 * @version 1.3.0
 * @date 2022-07-24
 *
 */

/**
 * @mainpage Avionics Loop
 * @section overview Overview
 *
 * This is the setup and process loop for the SilverSat Avionics Board.
 *
 * The on-board devices are implemented as classes interfacing to real hardware and include an external watchdog timer, external realtime clock, inertial measurement
 * unit, and FRAM. The board also includes serial ports, I2C buses, and a SAMD21 processor. The SAMD21 internal watchdog timer is not used.
 *
 * The other boards: Power, Radio, and Payload, are represented as classes which provide interfaces to encapsulate their functions.
 *
 * The beacon message which Avionics sends to the Radio Board, the command messages the Radio Board forwards to Avionics,
 * and the response and local command messages sent to the Radio Board are also represented as classes.
 *
 */

// todo: turn off instrumentation
#define INSTRUMENTATION // Instrumentation for processor and memory usage

#include "log_utility.h"
#include "PowerBoard.h"
#include "AvionicsBoard.h"
#include "RadioBoard.h"
#include "PayloadBoard.h"
#include "CommandProcessor.h"

/**
 * @brief Process loop constants
 *
 */
constexpr uint32_t serial_baud_rate{57600}; /**< speed of serial connection @hideinitializer */
// todo: adjust to 45 minutes for full test
constexpr unsigned long separation_delay{5 * seconds_to_milliseconds};

/**
 * @brief Create the boards and command processor
 *
 */

AvionicsBoard avionics{};
PowerBoard power{};
RadioBoard radio{};
PayloadBoard payload{};
CommandProcessor command_processor{};

#ifdef INSTRUMENTATION
/**
 * @brief Test instrumentation values
 *
 */

constexpr unsigned long serial_delay{2 * seconds_to_milliseconds};
unsigned long previous_time{};
unsigned long duration{};
unsigned long loop_start_time{};
unsigned long loop_maximum{0};
unsigned long loop_maximum_timestamp{};
unsigned long watchdog_maximum{0};
unsigned long watchdog_maximum_timestamp{};
unsigned long stability_maximum{0};
unsigned long stability_maximum_timestamp{};
unsigned long beacon_maximum{0};
unsigned long beacon_maximum_timestamp{};
unsigned long command_maximum{0};
unsigned long command_maximum_timestamp{};
unsigned long photo_maximum{0};
unsigned long photo_maximum_timestamp{};
unsigned long payload_maximum{0};
unsigned long payload_maximum_timestamp{};
long RAM_minimum{32768};
unsigned long RAM_minimum_timestamp{};
unsigned long display_start_time{};
constexpr int display_interval{5 * minutes_to_seconds * seconds_to_milliseconds};

/**
 * @brief Helper function for memory use
 *
 */
extern "C" char *sbrk(int i);

int FreeRam()
{
  char stack_dummy = 0;
  return &stack_dummy - sbrk(0);
}

#endif // INSTRUMENTATION

/**
 * @brief Initialize the devices and the boards
 *
 */

void setup()

{
  // Initialize serial connection and log utility

  Serial.begin(serial_baud_rate);
  // trigger the watchdog while waiting for the serial port
  unsigned long serial_delay_start{millis()};
  while ((millis() - serial_delay_start) < serial_delay)
  {
    avionics.trigger_watchdog();
  }
  // todo: turn off log facility
  Log.setPrefix(printPrefix);
  Log.setSuffix(printSuffix);
  Log.begin(LOG_LEVEL_INFO, &Serial);
  Log.setShowLevel(false);

  Log.noticeln("Initializing Avionics Process");

  // Initialize Avionics Board

  Log.noticeln("Initializing Avionics Board");
  avionics.begin();
  Log.noticeln("Avionics Board initialization completed");

  // Initialize Power Board

  Log.noticeln("Initializing Power Board interface");
  power.begin();
  Log.noticeln("Power Board interface initialization completed");

  // Initialize Radio Board

  Log.noticeln("Initializing Radio Board interface");
  radio.begin();
  Log.noticeln("Radio Board interface initialization completed");

  // Initialize Payload Board

  Log.noticeln("Initializing Payload Board interface");
  payload.begin();
  Log.noticeln("Payload Board interface initialization completed");

  // Wait for separation delay

  Log.noticeln("Beginning separation delay");
  unsigned long separation_timer_start{millis()};
  while ((millis() - separation_timer_start) < separation_delay)
  {
    avionics.trigger_watchdog();
  };
  Log.noticeln("Ending separation delay");

  // Deploy antenna

  Log.noticeln("Beginning antenna deployment");
  // todo: consider moving antenna to avionics loop
  avionics.deploy_antenna();
  Log.noticeln("Antenna deployment completed");

  // Initialization complete

  Log.noticeln("Avionics Process initialization completed");

#ifdef INSTRUMENTATION
  // Set up instrumentation

  loop_start_time = micros();
  display_start_time = millis();
#endif // INSTRUMENTATION
}

/**
 * @brief Execute the Avionics functions
 *
 */

void loop()
{

#ifdef INSTRUMENTATION
  previous_time = micros();
#endif // INSTRUMENTATION

  // Trigger the watchdog

  avionics.trigger_watchdog();

#ifdef INSTRUMENTATION
  duration = micros() - previous_time;
  if (duration > watchdog_maximum)
  {
    watchdog_maximum = duration;
    watchdog_maximum_timestamp = millis();
  }
  previous_time = micros();
#endif // INSTRUMENTATION

  // Determine stability

  // todo: consider checking on longer interval

  avionics.get_stability();

#ifdef INSTRUMENTATION
  duration = micros() - previous_time;
  if (duration > stability_maximum)
  {
    stability_maximum = duration;
    stability_maximum_timestamp = millis();
  }
  previous_time = micros();
#endif // INSTRUMENTATION

  // Send beacon

  avionics.check_beacon();

#ifdef INSTRUMENTATION
  duration = micros() - previous_time;
  if (duration > beacon_maximum)
  {
    beacon_maximum = duration;
    beacon_maximum_timestamp = millis();
  }
  previous_time = micros();
#endif // INSTRUMENTATION

  // Process command

  command_processor.check_for_command();

#ifdef INSTRUMENTATION
  duration = micros() - previous_time;
  if (duration > command_maximum)
  {
    command_maximum = duration;
    command_maximum_timestamp = millis();
  }
  previous_time = micros();
#endif // INSTRUMENTATION

  // Check for photo time

  avionics.check_photo();

#ifdef INSTRUMENTATION
  duration = micros() - previous_time;
  if (duration > photo_maximum)
  {
    photo_maximum = duration;
    photo_maximum_timestamp = millis();
  }
  previous_time = micros();
#endif // INSTRUMENTATION

  // Shut off Payload Board if ready to sleep

  payload.check_shutdown();

#ifdef INSTRUMENTATION
  duration = micros() - previous_time;
  if (duration > payload_maximum)
  {
    payload_maximum = duration;
    payload_maximum_timestamp = millis();
  }

  // Record free RAM

  auto free_RAM{FreeRam()};
  if (free_RAM < RAM_minimum)
  {
    RAM_minimum = free_RAM;
    RAM_minimum_timestamp = millis();
  }

  if (millis() - display_start_time > display_interval)
  {
    char timestamp[20]{};
    formatTimestamp(timestamp, loop_maximum_timestamp);
    Log.verboseln("Maximum loop time %l microseconds at %s", loop_maximum, timestamp);
    formatTimestamp(timestamp, watchdog_maximum_timestamp);
    Log.verboseln("Maximum watchdog processing duration %l microseconds at %s", watchdog_maximum, timestamp);
    formatTimestamp(timestamp, stability_maximum_timestamp);
    Log.verboseln("Maximum stability processing duration %l microseconds at %s", stability_maximum, timestamp);
    formatTimestamp(timestamp, beacon_maximum_timestamp);
    Log.verboseln("Maximum beacon processing time %l microseconds at %s", beacon_maximum, timestamp);
    formatTimestamp(timestamp, command_maximum_timestamp);
    Log.verboseln("Maximum command processing time %l microseconds at %s", command_maximum, timestamp);
    formatTimestamp(timestamp, photo_maximum_timestamp);
    Log.verboseln("Maximum photo processing time %l microseconds at %s", photo_maximum, timestamp);
    formatTimestamp(timestamp, payload_maximum_timestamp);
    Log.verboseln("Maximum payload processing time %l microseconds at %s", payload_maximum, timestamp);
    formatTimestamp(timestamp, RAM_minimum_timestamp);
    Log.verboseln("Minimum free RAM %l bytes at %s", RAM_minimum, timestamp);
    display_start_time = millis();
    Log.verboseln("Current free RAM %l bytes", FreeRam());
  }

  // Record loop time

  duration = micros() - loop_start_time;
  if (duration > loop_maximum)
  {
    loop_maximum = duration;
    loop_maximum_timestamp = millis();
  }
  loop_start_time = micros();
#endif // INSTRUMENTATION
}

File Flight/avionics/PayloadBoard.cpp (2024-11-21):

/**
 * @author Lee A. Congdon (lee@silversat.org)
 * @author Benjamin S. Cohen (ben@silversat.org)
 * @brief SilverSat Payload Board
 *
 * This file implements the class which interfaces with the Payload Board
 *
 */

#include "PayloadBoard.h"
#include "PowerBoard.h"
#include "Beacon.h"
#include "log_utility.h"

/**
 * @brief Payload Board constants
 *
 *
 */

constexpr int shutdown_delay{15 * seconds_to_milliseconds};
constexpr int maximum_cycle_time{10 * minutes_to_seconds * seconds_to_milliseconds};

/**
 * @brief Initialize Payload Board
 *
 * @return true successful
 * @return false error
 *
 */

bool PayloadBoard::begin()
{
    Log.traceln("Payload Board initializing");
    pinMode(PLD_ON_A_INT, OUTPUT);
    pinMode(PLD_ON_B_INT, OUTPUT);
    pinMode(PLD_ON_C_INT, OUTPUT);
    power_down();
    pinMode(STATES_A_INT, OUTPUT);
    pinMode(STATES_B_INT, OUTPUT);
    pinMode(STATES_C_INT, OUTPUT);
    pinMode(SHUTDOWN_A, INPUT);
    pinMode(SHUTDOWN_B, INPUT);
    pinMode(SHUTDOWN_C, INPUT);
    pinMode(PAYLOAD_OC, INPUT);
    Log.traceln("Payload Board initialization complete");
    return true;
}

/**
 * @brief Power up Payload Board and take photo
 *
 * @return true successful
 * @return false error
 *
 */

bool PayloadBoard::photo()
{
    if (!check_startup())
    {
        return false;
    }
    Log.noticeln("Starting photo session");
    set_mode_photo();
    power_up();
    return true;
}

/**
 * @brief Power up Payload Board and start SSDV
 *
 * @return true successful
 * @return false error
 *
 */

bool PayloadBoard::SSDV()
{
    if (!check_startup())
    {
        return false;
    }
    Log.noticeln("Starting SSDV session");
    set_mode_SSDV_start();
    power_up();
    return true;
}

/**
 * @brief Power up Payload Board and communicate
 *
 * @return true successful
 * @return false error
 *
 */

bool PayloadBoard::communicate()
{
    if (!check_startup())
    {
        return false;
    }
    Log.noticeln("Starting communication session");
    set_mode_comms();
    power_up();
    return true;
}

/**
 * @brief Verify Payload Board is ready to start
 *
 * @return true Payload Board is ready
 * @return false Payload Board is not ready
 */

bool PayloadBoard::check_startup()
{
    if (m_state != PayloadState::off)
    {
        Log.errorln("Payload already active");
        return false;
    }
    extern PowerBoard power;
    if (!power.power_adequate())
    {
        Log.errorln("Inadequate power for Payload session");
        return false;
    }
    return true;
}

/**
 * @brief Manage Payload Board state
 *
 *
 */
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

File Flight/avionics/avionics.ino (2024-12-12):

/**
 * @author Lee A. Congdon (lee@silversat.org)
 * @author Benjamin S. Cohen (ben@silversat.org)
 * @brief Avionics Board Setup and Process Loop
 *
 */

/**
 * @mainpage Avionics Loop
 * @section overview Overview
 *
 * This is the setup and process loop for the SilverSat Avionics Board.
 *
 * The on-board devices are implemented as classes interfacing to real hardware and include an external watchdog timer, external realtime clock, inertial measurement
 * unit, and FRAM. The board also includes serial ports, I2C buses, and a SAMD21 processor. The SAMD21 internal watchdog timer is not used.
 *
 * The other boards: Power, Radio, and Payload, are represented as classes which provide interfaces to encapsulate their functions.
 *
 * The beacon message which Avionics sends to the Radio Board, the command messages the Radio Board forwards to Avionics,
 * and the response and local command messages sent to the Radio Board are also represented as classes.
 *
 */

#include "log_utility.h"
#include "Antenna.h"
#include "PowerBoard.h"
#include "AvionicsBoard.h"
#include "RadioBoard.h"
#include "PayloadBoard.h"
#include "CommandProcessor.h"

// Avionics loop constants

constexpr uint32_t serial_baud_rate{19200}; /**< speed of serial connection @hideinitializer */
constexpr unsigned long serial_delay{2 * seconds_to_milliseconds};
constexpr unsigned long test_delay{30 * minutes_to_seconds * seconds_to_milliseconds};

// Create the boards, antenna, and command processor

AvionicsBoard avionics{};
PowerBoard power{};
RadioBoard radio{};
PayloadBoard payload{};
Antenna antenna{};
CommandProcessor command_processor{};

/**
 * @brief Arduino setup function to initialize the boards and devices and test them
 *
 */

void setup()
{
  // Initialize logging and the boards

  Serial.begin(serial_baud_rate);
  unsigned long serial_delay_start{millis()};
  while ((millis() - serial_delay_start) < serial_delay)
  {
    avionics.service_watchdog(); // service the watchdog while waiting for the serial port
  }
  Log.setPrefix(printPrefix);
  Log.setSuffix(printSuffix);
  Log.begin(LOG_LEVEL_VERBOSE, &Serial);
  Log.setShowLevel(false);
  Log.noticeln("Avionics software compiled %s at %s local time", __DATE__, __TIME__);

  Log.noticeln("Flight Software");
  Log.noticeln("Initializing Avionics Process");

  Log.noticeln("Initializing Avionics Board");
  if (avionics.begin())
  {
    Log.noticeln("Avionics Board initialization completed");
  }
  else
  {
    Log.errorln("Avionics Board initialization failed");
  }

  Log.noticeln("Initializing Power Board interface");
  if (power.begin())
  {
    Log.noticeln("Power Board interface initialization completed");
  }
  else
  {
    Log.errorln("Power Board interface initialization failed");
  }

  Log.noticeln("Initializing Radio Board interface");
  if (radio.begin())
  {
    Log.noticeln("Radio Board interface initialization completed");
  }
  else
  {
    Log.errorln("Radio Board interface initialization failed");
  }

  Log.noticeln("Initializing Payload Board interface");
  if (payload.begin())
  {
    Log.noticeln("Payload Board interface initialization completed");
  }
  else
  {
    Log.errorln("Payload Board interface initialization failed");
  }

  Log.noticeln("Initializing Antenna");
  if (antenna.begin())
  {
    Log.noticeln("Antenna initialization completed");
  }
  else
  {
    Log.errorln("Antenna initialization failed");
  }
  
  Log.noticeln("Setup complete");

  // Test delay

  Log.noticeln("Starting test delay");
  unsigned long test_delay_start{millis()};
  while ((millis() - test_delay_start) < test_delay)
  {
    avionics.service_watchdog(); // service the watchdog during the test delay
  }
  Log.noticeln("Test delay complete");
  Log.noticeln("Avionics process accepting commands");

  // Testing: test the devices and the boards

  Log.noticeln("Testing satellite components");

  Log.noticeln("Verifying external realtime clock status");
  avionics.test_external_rtc();

  Log.noticeln("Testing IMU");
  avionics.test_IMU();

  Log.noticeln("Testing FRAM");
  avionics.test_FRAM();

  Log.noticeln("Testing EPS-I");
  power.test_EPS();

  Log.noticeln("Testing Radio");
  radio.test_radio();

  Log.noticeln("Testing Payload");
  payload.photo();

  Log.noticeln("Testing Antenna");
  antenna.test_antenna();

  Log.noticeln("Initial testing complete, Radio and Payload tests continue");
}

/**
 * @brief Arduino loop function to execute the Avionics functions
 *
 */

void loop()
{
  updateLogDay();
  avionics.service_watchdog();
  antenna.check_antenna();
  avionics.get_stability();
  avionics.check_beacon();
  command_processor.check_for_command();
  avionics.check_payload();
  payload.check_shutdown();
}

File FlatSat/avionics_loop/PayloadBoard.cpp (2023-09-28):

/**
 * @file PayloadBoard.cpp
 * @author Lee A. Congdon (lee@silversat.org)
 * @brief SilverSat Payload Board
 * @version 1.1.1
 * @date 2022-07-24
 *
 * This file implements the class which interfaces with the Payload Board
 *
 */

#include "PayloadBoard.h"
#include "PowerBoard.h"
#include "log_utility.h"

/**
 * @brief Payload Board constants
 *
 *
 */

constexpr int startup_delay{90 * seconds_to_milliseconds};
constexpr int shutdown_delay{15 * seconds_to_milliseconds};
constexpr int maximum_cycle_time{10 * minutes_to_seconds * seconds_to_milliseconds};

/**
 * @brief Initialize Payload Board
 *
 * @return true successful
 * @return false error
 *
 */

bool PayloadBoard::begin()
{
    Log.traceln("Payload Board initializing");
    pinMode(PLD_ON_A_INT, OUTPUT);
    pinMode(PLD_ON_B_INT, OUTPUT);
    pinMode(PLD_ON_C_INT, OUTPUT);
    pinMode(STATES_A_INT, OUTPUT);
    pinMode(STATES_B_INT, OUTPUT);
    pinMode(STATES_C_INT, OUTPUT);
    pinMode(SHUTDOWN_A, INPUT);
    pinMode(SHUTDOWN_B, INPUT);
    pinMode(SHUTDOWN_C, INPUT);
    pinMode(PAYLOAD_OC, INPUT);
    power_down();
    Log.traceln("Payload Board initialization complete");
    return true;
}

/**
 * @brief Power up Payload Board and take photo
 *
 * @return true successful
 * @return false error
 *
 */

bool PayloadBoard::photo()
{
    if (m_payload_active)
    {
        Log.errorln("Payload already active");
        return false;
    }
    extern PowerBoard power;
    if (!power.power_adequate())
    {
        Log.errorln("Inadequate power for photo session");
        return false;
    }
    Log.noticeln("Starting photo session");
    set_mode_photo();
    power_up();
    return true;
}

/**
 * @brief Power up Payload Board and communicate
 *
 * @return true successful
 * @return false error
 *
 */

bool PayloadBoard::communicate()
{
    if (m_payload_active)
    {
        Log.errorln("Payload already active");
        return false;
    }
    extern PowerBoard power;
    if (!power.power_adequate())
    {
        Log.errorln("Inadequate power for communications session");
        return false;
    }
    Log.noticeln("Starting Communication session");
    set_mode_comms();
    power_up();
    return true;
}

/**
 * @brief Shut off Payload Board if ready to sleep
 *
 * @return true successful
 * @return false error
 *
 */

bool PayloadBoard::check_shutdown()
{
    // check shutdown signal after startup delay
    if (m_payload_active && (millis() - m_payload_start_time > startup_delay))
    {
        auto shutdown_a{digitalRead(SHUTDOWN_A)};
        auto shutdown_b{digitalRead(SHUTDOWN_B)};
        auto shutdown_c{digitalRead(SHUTDOWN_C)};
        m_shutdown_signal_was_set = m_shutdown_signal_was_set || (shutdown_a + shutdown_b + shutdown_c >= 2);
    }
    // if shutdown signal received, shutdown payload after shutdown delay
    if (m_shutdown_signal_was_set)
    {
        if (m_in_shutdown_delay)
        {
            if (millis() - m_shutdown_start_time > shutdown_delay)
            {
                Log.verboseln("Powering down payload");
                power_down();
            }
        }
        else
        {
            Log.verboseln("Starting payload shutdown delay");
            m_in_shutdown_delay = true;
            m_shutdown_start_time = millis();
        }
    }
    // check for Payload Board timeout
    if (m_payload_active && (millis() - m_payload_start_time > maximum_cycle_time))
    {
        Log.errorln("Payload cycle too long");
        power_down();
        m_timeout_occurred = true;
        return false;
    }
    // check for Payload Board over current (active low)
    if (m_payload_active && !digitalRead(PAYLOAD_OC))
    {
        Log.errorln("Payload over current");
        power_down();
        m_last_payload_activity = LastPayloadActivity::overcurrent;
        m_overcurrent_occurred = true;
        return false;
    }
    return true;
}

/**
 * @brief Power down Payload Board
 *
 * @return true successful
 * @return false error
 *
 */

bool PayloadBoard::power_down()
{
    digitalWrite(PLD_ON_A_INT, HIGH);
    digitalWrite(PLD_ON_B_INT, HIGH);
    digitalWrite(PLD_ON_C_INT, HIGH);
    m_payload_active = false;
    m_shutdown_signal_was_set = false;
    m_in_shutdown_delay = false;
    m_last_payload_duration = millis() - m_payload_start_time;
    Log.verboseln("Payload power off");
    return true;
}

/**
 * @brief Power up Payload Board
 *
 * @return true successful
 * @return false error
 *
 */

bool PayloadBoard::power_up()
{
    digitalWrite(PLD_ON_A_INT, LOW);
    digitalWrite(PLD_ON_B_INT, LOW);
    digitalWrite(PLD_ON_C_INT, LOW);
    m_timeout_occurred = false;
    m_overcurrent_occurred = false;
    m_payload_active = true;
    m_payload_start_time = millis();
    Log.verboseln("Payload power on");
    return true;
}

/**
 * @brief Set the mode to communications
 *
 * @return true successful
 * @return false error
 *
 */
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

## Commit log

2022-03-27 Variant
    These are the variant files for the Metro M0 Express to add 2 extra serial ports and 1 extra wire port.
2022-03-27 Create MetroVariantTest.fzz
    Fritzing file to show how to connect up the Metro M0 express for testing
    [MetroVariantTest.fzz]
2022-05-20 Prototype FRAM test in Python
2022-05-22 Arduino FRAM test prototype
2022-06-03 Fix for Arduino UNO
2022-06-06 Initial board test suite
2022-06-29 Convert bus switch mocking software to library
2022-06-30 Update Bus Switch Mock Library
2022-06-30 Implement Mock Watchdog Timer
2022-07-11 Board, SAMD21, Watchdog, I2C, Bus Switch
2022-07-11 Bus Switch, FRAM, I2C and IMU
2022-07-11 Disconnect mock IMU from Adafruit libraries
2022-07-12 Integrated external RTC in mock board test
2022-07-21 Test IMU
2022-07-21 I2C switch
2022-07-24 Use mock boards in process loop
2022-07-30 Create command queue for mock radio board
2022-07-31 Implement ArduinoLog
2022-08-05 Create power unit test
2022-08-11 Non-critical I2C, busswitch, refactor external RTC
2022-08-11 Implement noncrit-I2C, refactor
2022-08-12 Change timing to milliseconds
2022-08-13 Update I2C enable logic
2022-08-22 Get beacon interval, photo count, comms, power
2022-09-01 Initial ground implementation
2022-09-02 Working ground version
2022-09-22 Frame commands with KISS
2022-09-22 Implement halt and deploy antenna
2022-09-24 Bug fix for String length
    [hex2bin.ino]
2022-10-14 Board testing
2022-10-17 Adjust code to enable Avionics Board
2022-10-17 Change serial print to logging
2022-10-18 Add delay and error checks for realtime clock
    [AvionicsBoard.cpp]
2022-10-19 Add LED test software
2022-10-19 Update variants
    [MetroVariantTest.fzz]
2022-10-19 Validate LED D5
2022-10-25 Add board interfaces
2022-10-28 Update power and beacon
2022-10-29 Add I2C Scan
2022-12-08 Correct power board status
2022-12-14 Implement internal watchdog timer
2023-01-07 Add switch example
2023-01-29 Rename mock board files
2023-02-02 Update Avionics Board functional tests
2023-02-03 Update Avionics Board tests
2023-02-06 Create framework
2023-02-27 Update Payload Board, add emulator
2023-03-18 Update PayloadBoard.cpp
    Swapped order of delays
    [PayloadBoard.cpp]
2023-03-20 Correct trailing blank bug
    [tokenizer.ino]
2023-03-28 Remove Radio Board status
2023-03-28 Fix compiler and cppcheck issues
    [RadioBoard.cpp]
2023-04-13 Refactor message sending and errors
    [Antenna.cpp, AvionicsBoard.cpp, RadioBoard.cpp]
2023-04-16 Update power board implementation
2023-04-16 Update power board
2023-05-08 Disable I2C scan for DS1337
2023-05-08 Smooth MPU6050 data for stability test
    [AvionicsBoard.cpp]
2023-05-08 Handle runaway Payload Board and timer wrap
2023-05-09 Add error flags and modify Power and Payload
    [AvionicsBoard.cpp, PayloadBoard.cpp, avionics_loop.ino]
2023-06-09 Improve antenna simulator
2023-06-12 Verify adequate power for payload session
2023-06-27 Display pin state
2023-06-28 IMU constructor
2023-08-28 Scan for I2C devices on startup
2023-08-30 Send antenna recovery messages to Radio
2023-09-01 Add LUP 5V data to GetPower
2023-09-01 Simplify watchdog reset command
    [AvionicsBoard.cpp]
2023-09-10 Clear I2C buses
2023-09-11 Enable FlatSat I2C interface
2023-12-11 Updates from antenna test
2023-12-17 Ground software README
2024-02-03 Update ground station appearance
2024-03-13 Restructure and move ground software to new repository
2024-03-17 Fix command content concatenation in Response class and update radio status pattern
    [RadioBoard.cpp]
2024-03-18 Update instrumentation, log level, and power down message
2024-06-23 Update antenna delay for flight to 80 seconds, startup to 45 minutes
2024-07-27 cycle 5v command
2024-08-07 Test cases for refactored receive frame
2024-08-07 Add command to cycle 5V power
2024-08-24 Serial monitor speed fix
    [RadioBoard.cpp, avionics.ino]
2024-08-27 Correct radio receive code
    [RadioBoard.cpp]
2024-10-05 restore paylod voltage minimum
2024-10-05 initial battery voltage in log
2024-10-05 changed imu calibration
2024-10-05 turn on 5v turn 3.3v LUPS
2024-10-06 Correct 5VLUP and 3V3LUP line settings
    [RadioBoard.cpp, avionics.ino]
2024-10-08 Depoy antenna in main loop
2024-10-11 Correct SSDV start condition
    [PayloadBoard.cpp]
2024-10-12 Add IMU test
2024-10-13 Add antenna test
2024-10-20 Supress remote messages if antenna cycle incomplete
2024-10-24 Fix antenna deployment bugs
    [Antenna.cpp, avionics.ino]
2024-10-26 Shorten separation and antenna delays for testing
2024-11-05 Enhance avionics initialization with error handling and logging
    [avionics.ino]
2024-11-11 Modify timeout defaults in Antenna and CommandProcessor; omit frequence prompt
2024-11-17 Update command port, modify payload beacon enums, and refactor payload board state management
2024-11-17 Refactor antenna deployment logging and remove unused delay variable
2024-11-18 Refactor antenna delay handling and update bypass messages
2024-11-18 Add external power handling to PowerBoard class
2024-12-07 changed callibration for the imu
2024-12-09 Update IMU calibration constants and change command port for serial communication
2024-12-12 Enhance logging and initialization for antenna; set beacon interval to off and add test delay in setup
